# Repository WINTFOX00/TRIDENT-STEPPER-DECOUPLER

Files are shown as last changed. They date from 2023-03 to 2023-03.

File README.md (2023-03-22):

# TRIDENT-STEPPER-DECOUPLER

**STEPPER DECOUPLER FOR VORON TRIDEN**

Stepper decoupler for Nema17 motors. Reduce VFA, make it smoother, quieter, and more sturdy- get rid of the risk of curving the step shaft due to running at high acceleration for a long time.



https://user-images.githubusercontent.com/58668874/226819730-55bcf3cf-9251-406a-b716-160ee1cf82bb.mp4

----------------------------

***ATTENTION: This MOD is made for original A/B drive, not tested for compatibility with other mods, eg Umbilical Mod...***

BOM :

+ 2 X D20L30 double diaphragm coupler | https://aliexpi.com/lwOQ

+ 2 Round D Shaft 55x5mm (longer still OK) | https://aliexpi.com/miUU

+ 4 X M3 75mm hex screw | https://aliexpi.com/bF7d

+ 2 x M3 30mm hex screw (use original screws)

+ 4 x M3 6mm hex screw.

+ 4 X 695 2RS bearing | https://aliexpi.com/YE7s

+ 2 X NEMA 17 Stepper Vibration Damper | https://aliexpi.com/2EX7
 
+ 2 X M3 brass insert nut (OD4.5, 3, 4 or 5mm length is ok) | https://aliexpi.com/Onkg



**ASSEMBLE**

You don't need to disassemble the entire A/B drive, just loosen the belt, remove the stepper mounting screws, and add components. I can mount this mod without removing the A/B from the frame with a little trick (not recommended)

***THIS IS THE INSTALLATION STEPS FOR B-DRIVE. YOU CAN INSTALL A-DRIVE IN THE SAME WAY.



1/ Insert 2 bearings into the plastic part



2/ Add heat insert nut



3/ Remove 3 M3 screws on B Drive. Be careful not to let the stepper fall ( *Extra reminder for sure : No need to disassemble idler bearings*)



4/ Install the step damper, pay attention to the orientation



5/ Assemble the Coupler, Spacer, Idler in the order shown in the picture. Do not tighten the screw, because it still needs to be adjusted.



6 /Insert the Stepper into the B-Drive, tighten the screws.





7/ Adjust the Puller according to the bearing idler.



**This is the final step. You can continue to assemble side A with the same steps. Re-tension the belt, recalibrate the Input Shaper and Enjoy !**

Test print result (Click to view fullsize for correct display) : 



**Feel free to contact me if there is any problem**

Discord : Wintfox#0709

**Thanks for stopping by !**

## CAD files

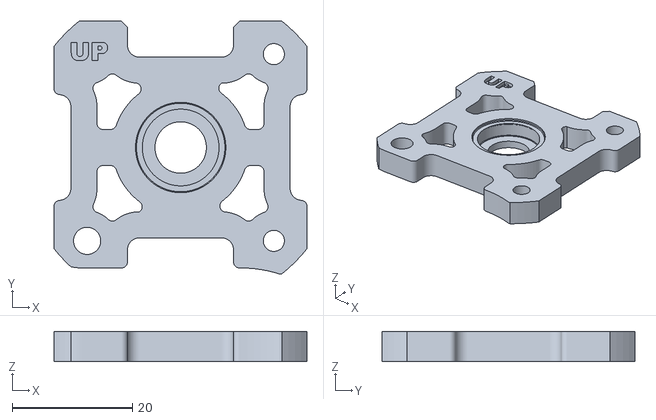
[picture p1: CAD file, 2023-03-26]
STL/Bottom Bearing-A.stl
42.0 x 42.0 x 5.00

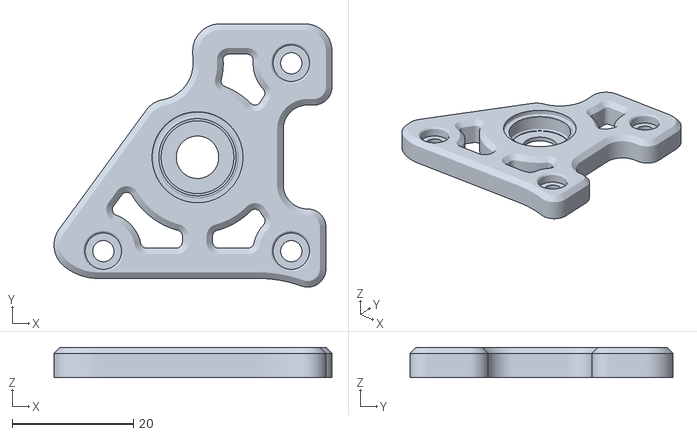
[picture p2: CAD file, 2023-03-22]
STL/Top Bearing-A.stl
45.9 x 43.4 x 5.00

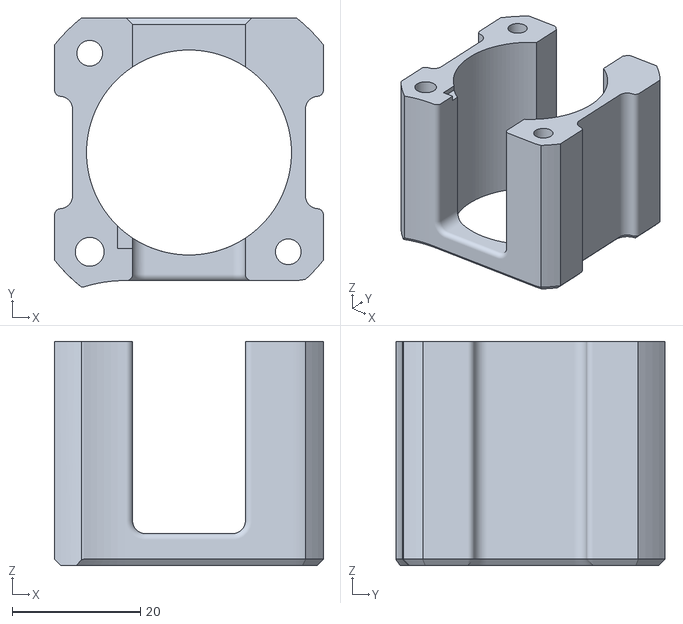
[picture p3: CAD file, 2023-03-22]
STL/Spacer-B.stl
42.0 x 42.0 x 35.0

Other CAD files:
STL/Bottom Bearing-B.stl
STL/Top Bearing-B.stl
STL/Spacer-A.stl

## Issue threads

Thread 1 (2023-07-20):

M3 75mm!

brianvoe, 2023-07-20:
Love the design. In the process of building mine.

I understand why its 75 but if there is any way to break it up in a way that you can do like 2 25mm. The issue being the only way to get that length is to order them from china and wait 3 weeeks.

atoomnetmarc, 2023-11-03:
For me ordering 75mm M3 and waiting was no problem. It was only a week and a bit. I can see why the 75mm was used with the existing parts.

brianvoe, 2023-11-03:
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

I came up with a bit of a different design. It still requires 8 55mm length m3 which is still not ideal.

Let me know your thoughts.

brianvoe, 2023-11-03:
Im also running 9mm belts so the height between plates is higher than normal

pasha4ur, 2024-01-08:
> Im also running 9mm belts so the height between plates is higher than normal

Hello

Can you share you solution for 9mm belts, please?

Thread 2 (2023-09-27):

Insert position wrong!

nexposito, 2023-09-27:
Hello, I printed the parts to make the mod and I noticed that insert position in Bottom Bearing-A is wrong.

WINTFOX00, 2023-09-27:
Thanks for the heads up, I just checked again and it's still in place. Can
you please provide me with more pictures? thank you :D

*HO HUYNH* | Freelancer Illustrator

----------------------------------------------

*https://www.artstation.com/fox* <https://www.artstation.com/fox>

On Wed, Sep 27, 2023 at 10:04 AM Nicolas Exposito ***@***.***>
wrote:

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

atoomnetmarc, 2023-11-03:
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

mstaniszczak, 2023-11-23:
Maybe Bottom Bearing-B upside down will fit. I will  check tomorrow, but you have right, hole for insert is in wrong place.

mstaniszczak, 2023-11-23:
Ah no... Bearing will be also upside down...

mstaniszczak, 2023-11-23:
The step file looks like the screw is screwed directly into the plastic?
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

WINTFOX00, 2023-11-23:
Sorry for the inconvenience. I've been a bit busy with work so I haven't updated yet.

Yes, that part has the wrong heat insert orientation. But you can ignore it and insert it into the opposite hole, you can insert it directly or use a 4mm drill bit to make it a little wider.

mstaniszczak, 2023-11-24:
I added fix in https://github.com/WINTFOX00/TRIDENT-STEPPER-DECOUPLER/pull/6 :)

mstaniszczak, 2023-11-24:
@nexposito can you check if it fit also for you?

mstaniszczak, 2023-11-24:
Looks done now
![Uploading IMG_20231124_232700677.jpg…]()

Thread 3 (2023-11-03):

Does not fit: '2 x M3 30mm hex screw (use original screws)'

atoomnetmarc, 2023-11-03:
The '2 x M3 30mm hex screw (use original screws)' do not fit, they are about 5 mm too short. I used M3x40, they fit.

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

atoomnetmarc, 2023-11-03:
> they are about 5 mm too short.

Replying to myself. Actually M3x35 would also not fit. M3x38 would fit perfect. M3x40 is fine:

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

mstaniszczak, 2023-11-24:
Yes, it can't be oryginal screw. It is screwed in slightly higher and have to be screwed into insert, do deeper than oryginal. M3 40mm is fine - even if is too long it's invisible.

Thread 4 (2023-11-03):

Warning: D shaft from aliexpress link rattle around in bearings.

atoomnetmarc, 2023-11-03:
Hi, maybe I was unlucky, but the shafts from the Aliexpress link are too small. They rattle around in the bearings.

'2 Round D Shaft 55x5mm (longer still OK) | https://aliexpi.com/miUU'

All shafts are about 4.95mm or 4.96mm.
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

Bearing is 5mm.
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

I had an old shaft laying around that measured 4.99mm and that fit just perfectly in the bearing. However, I had just 1 and it was too short.

Not really an issue for your awesome mod, just a warning for others to be aware.

WINTFOX00, 2023-11-03:
Thank you for your reports. I'm on vacation so I'll check back in a few
days.
Btw, about the shaft, it's probably due to the (bad) quality fluctuations
from the manufacturer, the one I bought fits perfectly. You can fix it by
wrapping it in a few layers of kapton tape.

*HO HUYNH* | Freelancer Illustrator

----------------------------------------------

*https://www.artstation.com/fox* <https://www.artstation.com/fox>

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

atoomnetmarc, 2023-11-07:
I have ordered 2 pieces of German made 5mm (DIN 175 specification) round 500mm long silver steel rods and have cut them to length. They are much more close to 5mm (4.98mm). I figured that D-shaft maybe not be the best solution under tension of the belts unless they are some kind of friction fit. Round shaft are not able to rattle.

Will let you know how this work out once I mounted them. Maybe I should cut a little flat spot for the grub screw of the pulleys if they slip.

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

atoomnetmarc, 2023-11-08:
I have retried the assembly with the round 5mm shafts. They do not rattle. Time will tell if I need a flat spot for the pulleys.

I measured the noise (in peak dBA) of moving the printing head from left to right and back before the mod and after the mod.
Subjective there is not much difference in noise level. I noticed that my printer has noise peaks at 25, 50 and 100 mm/s.

According to my UNI-T UT353 dBA meter the average noise dropped a tiny bit from 48.5dBA to 47.3dBA.

Graph:

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

For me this issue can be closed. Switching from Aliexpress d-shaft monday morning special to German made round shaft solved the rattle.

WINTFOX00, 2023-11-09:
Hello. I just returned from vacation.
Thank you very much for the feedback. I will spend time improving and
fixing errors.
P/s: Regarding noise level, I don't have a specialized measuring device
yet, but with my printer using a 0.9 degree stepper, it almost makes the
printer silent, even with 8 microstepping + no stealthchop :D
Thank you again and have a nice day :D

*HO HUYNH* | Freelancer Illustrator

----------------------------------------------

*https://www.artstation.com/fox* <https://www.artstation.com/fox>

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

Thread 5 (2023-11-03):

Consider adding a license

atoomnetmarc, 2023-11-03:
Hi,

Please consider adding a file named `LICENSE`, with the chosen license. If someone (like https://github.com/brianvoe in https://github.com/WINTFOX00/TRIDENT-STEPPER-DECOUPLER/issues/1) chooses to make a fork and apply modifications, that makes it easier to know what you can do with it.

Depending If you used Voron source material you probably must choose the same license (https://github.com/VoronDesign/Voron-Trident/blob/main/LICENSE) or you can choose whatever license suits you. I am a fan of Apache 2 (https://github.com/atoomnetmarc/Yet-another-shitty-carbon-filter/blob/main/LICENSE). However, I am not a lawyer so I cannot advise you to choose one.

WINTFOX00, 2023-11-03:
Thank you for your suggestion.
I'm just an amateur 3D printer user so I don't know much about this. I'll
figure it out when I get back to work.
Thanks again and have a nice day :D

*HO HUYNH* | Freelancer Illustrator

----------------------------------------------

*https://www.artstation.com/fox* <https://www.artstation.com/fox>

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

brianvoe, 2023-11-03:
Adding a license is a good idea. Also I have no interest in making changes to yours and calling it my own. The design is already great as it is.

mstaniszczak, 2023-11-25:
+1. If you want gpl3 like voron, I can prepare for you pull request with it😉

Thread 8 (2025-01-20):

Ballscrews?

Killajoedotcom, 2025-01-20:
What is the ball screw mod you have going on here? Could you link to that in readme?

WINTFOX00, 2025-01-20:
I made it myself. And after a pretty tiring process to get it working I
found it wasn't worth the money and time spent compared to the benefits so
I didn't think I should share it.

* HO HUYNH* | Freelancer Illustrator

----------------------------------------------

 *https://www.artstation.com/fox* <https://www.artstation.com/fox>

On Mon, Jan 20, 2025 at 9:58 PM Killa_Prints ***@***.***>
wrote:

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

Closed 2025-01-20.

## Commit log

2023-03-22 Create STL
2023-03-22 Rename PRINTABLE/Link to PRINTABLES/Printables Link
